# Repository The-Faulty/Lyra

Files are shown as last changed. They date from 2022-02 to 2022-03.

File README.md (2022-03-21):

# Lyra

**A SamD21 Based Rocket Deployment Altimeter**

This altimeter will be able to be used for single deployment events in mid to high power rocketry. A compact design was emphasized in order to allow for use in 24mm and larger body tubes, or attached to the parachute for a cable cutter or similar deployment method.

## Current State

As of right now, I am working on flight software with basic functionality. The original PCB design is filled with many flaws, however, I still included them for use as a reference. Plans have been made for a new version of the PCB to fix many, if not all, of the shortcomings my original design had. I believe I have found most of them, but one includes the difficulty of updating firmware and testing, which will inevitably lead to something being overlooked. Also to come are some pictures of the one prototype board that I have assembled. The changelog below is more to keep track of what I have or haven't tackled yet, so feel free to ignore it.

I have now successfully uploaded a version of the code to a Lyra board. One thing I did was replace the buzzer on the board with a bodged LED. This will allow for silent debugging and a guarantee that the lines are working. *This is the purpose of any digital writes to the buzzer pin.* The code that I uploaded ran until it attempted connection with the barometer in the setup. I will look further into the issue at a later point in time.

## The Bad, the Worse, and the Annoying

During my initial development of the Lyra pcb, I made some naive choices in terms of design, and overlooked other quality of life aspects which have led to many headaches during development. I'm going to go into some of the things that I have identified as issues in the current design or things I want to add in the next one.

The biggest issue that I made in the design of this pcb was not using a USB port. I figured that as long as I had the SWD I would be fine, but it just complicates development because I can't have the flash and SD card board attached at the same time. Another issue is lack of physical indicators. having LEDs on the power lines, pyro lines, and just attached to a GPIO pin would have helped a lot in diagnosing issues. Instead of using the BMP388, a barometer that I have used before and knew worked, I chose the MS5607 for Lyra. I don't remember why I made that choice, but the MS5607 has a few downsides compared to the BMP388. For one, there is no data ready register. This means that your code has to blindly wait for the reading to be completed, and then check back after. The libraries for using this sensor are also less tested than those for the BMP388. I also did not think very hard about the use of Lyra during an actual launch. I planned for the code to read a settings file from the SD card at launch, however, if I planned on using Lyra in multiple rockets or adjust settings on the go, I would have to bring a laptop. On the next itteration, one solution would be to use an oled shield, such as the adafruit feather oled, with a simple menu system for settings and readout. Finally, I wish I had broken out more pins to the daughter pcb. I didn't use all of the pins on the connector, and could have broken out I2C lines or similar for further prototyping.

## Changelog

Latest Changes:

**V0.2 - "Hands up, Don't Chute!"**

Notes: I think that most of the program is here, just need to do the loop logic. I also want to add data logging to the start of the flight.

- Fixed typo of `stateMacine` to `stateMachine`
- Fixed `state` being initialized as an integer instead of an instance of the `stateMachine` enum
- Fixed lack of function prototypes

- Changed `loop()` to use switch/case instead of `if else`
- Moved `readAlt()` to the start of if statement instead of in each case

- Added `ISDROGUE` and `ISAPOGEEDEPLOY` to user variables (I missed them in the last update)
- Added `DEPLOYALT` variable for setting the deployment altitude
- Added `SAVEDATA` boolean to toggle saving data to flash
- Added use of buzzer in `setup()` for indicating barometer found and setup complete
- Added `landed` case to `loop()`
- Added `rollPeriod` and `rollVelo` for use in velocity and acceleration calculations
- Added `calcAccel` for acceleration

**V0.1 - "No Function Junction"**

- Fixed variables being logged being out of order
- Fixed barometer code to use correct barometer model
- Fixed `readAlt()` function's for loop running until greater than the array's index
- Fixed not changing state from `startUp` to `idle` in setup

- Removed variable `rateLeng` and instead directly used the `rollAvg` array for vertical speed calculation

- Changed user-defined variables to be under define tags to allow usage in declaring array lengths

- Added vertical speed function (`getRate()`) and `avgRate` variable
- Added battery voltage function (`getBattVoltage()`)
- Added vertical speed to logging data
- Added `period` and `lastMillis` variables for tracking loop cycles
- Added majority of this ReadMe

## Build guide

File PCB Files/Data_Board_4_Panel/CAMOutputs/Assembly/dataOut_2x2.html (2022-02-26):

Partlist exported from C:/Users/andyd/Documents/EAGLE/projects/FC/Lyra/Panels/dataOut_2x2.sch at 10/29/2020 5:32 PM

Qty | Value | Device | Package | Parts | Description | BUILT_BY | COPYRIGHT | DESCRIPTION | DIGI-KEY_PART_NUMBER | MANUFACTURER_PART_NUMBER | MF | MP | PACKAGE | PROD_ID | PURCHASE-URL | SOURCELIBRARY | VALUE | VENDOR
4 | .1uF | 10NF-0603-50V-10% | 0603 | C1, C6, C8, C10 | 0.01uF/10nF/10,000pF ceramic capacitors | | | | | | | | | CAP-00867 | | | 10nF
4 | 10M | 220KOHM-0603-1/10W-1% | 0603 | R1, R3, R4, R5 | 220kΩ resistor | | | | | | | | | RES-08969 | | | 220k
4 | 12POS_HEADER | 12POS_HEADER | 12POS_HEADER | U$1, U$3, U$4, U$5
4 | 22pF | 10NF-0603-50V-10% | 0603 | C2, C5, C7, C9 | 0.01uF/10nF/10,000pF ceramic capacitors | | | | | | | | | CAP-00867 | | | 10nF
4 | 503182-1852 | 503182-1852 | MOLEX_503182-1852 | J1, J3, J4, J5 | Conn Micro SD Card M 8 POS 1.09mm Solder RA SMD Embossed T/R 0.5A/Contact | | | 10 (8 + 2) Position Card Connector microSD™ Surface Mount, Right Angle Gold | WM12834CT-ND | | Molex | 5031821852 | None | | https://pricing.snapeda.com/search/part/5031821852/?ref=eda
4 | S25FL064LABNFI043USON-8-M | S25FL064LABNFI043USON-8-M | USON-8-M | U1, U3, U4, U5 | | EMA_Jessica | Copyright (C) 2018 Accelerated Designs. All rights reserved | | | S25FL064LABNFI043 | | | | | | Cypress_Semiconductor_2019-12-17 | | Cypress Semiconductor

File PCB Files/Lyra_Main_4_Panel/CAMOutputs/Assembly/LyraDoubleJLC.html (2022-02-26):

Partlist exported from C:/Users/andyd/Documents/EAGLE/projects/FC/Lyra/Extras/LyraDoubleJLC.sch at 10/29/2020 7:39 AM

Qty | Value | Device | Package | Parts | Description | ARROW_ELECTRONICS-PURCHASE-URL | AVAILABILITY | BUILT_BY | COMMENT | COPYRIGHT | CUI_PURCHASE_URL | DESCRIPTION | DIGI-KEY_PART_NUMBER | DIGIKEY-PURCHASE-URL | EU_ROHS_COMPLIANCE | MANUFACTURER_PART_NUMBER | MF | MOUSER-PURCHASE-URL | MP | PACKAGE | PRICE | PROD_ID | PURCHASE-URL | SOURCELIBRARY | VALUE | VENDOR
20 | 0.1uF | 0.1UF-0603-25V-(+80/-20%) | 0603 | C1, C2, C4, C5, C8, C21, C22, C24, C25, C28, C41, C42, C44, C45, C48, C61, C62, C64, C65, C68 | 0.1µF ceramic capacitors | | | | | | | | | | | | | | | | | CAP-00810 | | | 0.1uF
4 | 0.22uF | 0.1UF-0603-25V-(+80/-20%) | 0603 | C3, C23, C43, C63 | 0.1µF ceramic capacitors | | | | | | | | | | | | | | | | | CAP-00810 | | | 0.1uF
8 | 1.0uF | 1.0UF-0402-16V-10% | 0402 | C11, C12, C29, C30, C49, C50, C69, C70 | 1µF ceramic capacitors | | | | | | | | | | | | | | | | | CAP-12417 | | | 1.0uF
4 | 100k | RESISTOR0402 | 0402 | R7, R27, R51, R75 | Generic Resistor Package
12 | 10k | RESISTOR0402 | 0402 | R4, R5, R9, R25, R29, R33, R49, R53, R57, R73, R77, R81 | Generic Resistor Package
4 | 12POS_SOCKET | 12POS_SOCKET | 12POS_SOCKET | U$5, U$15, U$25, U$35
4 | 180K | RESISTOR0402 | 0402 | R11, R35, R59, R83 | Generic Resistor Package
4 | 1k | RESISTOR0402 | 0402 | R8, R28, R52, R76 | Generic Resistor Package
8 | 20K | RESISTOR0402 | 0402 | R10, R12, R34, R36, R58, R60, R82, R84 | Generic Resistor Package
4 | 30 | RESISTOR0402 | 0402 | R1, R30, R54, R78 | Generic Resistor Package
4 | 32.768KHz | FC-135 | FC-135 | U$1, U$12, U$22, U$32
8 | 4.7k | 4.7KOHM-0603-1/10W-1% | 0603 | R2, R3, R31, R32, R55, R56, R79, R80 | 4.7kΩ resistor | | | | | | | | | | | | | | | | | RES-07857 | | | 4.7k
4 | 470k | RESISTOR0402 | 0402 | R6, R26, R50, R74 | Generic Resistor Package
8 | 7 pF | 0.1UF-0402-16V-10% | 0402 | C6, C7, C26, C27, C46, C47, C66, C67 | 0.1µF ceramic capacitors | | | | | | | | | | | | | | | | | CAP-12416 | | | 0.1uF
4 | ATSAMD21G18A-MU | ATSAMD21G18A-MU | QFN50P700X700X90-49N | U1, U5, U9, U13 | Cortex-M0+, 256KB FLASH, 32KB SRAM, USB, DMA, T&R - 48QFN IND TEMP, GREEN, 1.6-3.6V, 48MHz/ QFN (ZA) | https://snapeda.com/shop?store=Arrow+Electronics&id=590181 | | | | | | ARM® Cortex®-M0+ SAM D21G Microcontroller IC 32-Bit 48MHz 256KB (256K x 8) FLASH 48-QFN (7x7) | ATSAMD21G18A-MUTTR-ND | https://snapeda.com/shop?store=DigiKey&id=590181 | | | Microchip | https://snapeda.com/shop?store=Mouser&id=590181 | ATSAMD21G18A-MU | QFN-48 Microchip
4 | BUTTON | BUTTON | BUTTON | U$4, U$14, U$24, U$34
4 | CPT-1255C-090 | CPT-1255C-090 | CUI_CPT-1255C-090 | LS2, LS3, LS5, LS7 | Buzzer 12 mm, 20 Vp-p, 80 dB, Through Hole, Piezo Audio Transducer Buzzer Check prices | | Good | | | | https://www.cuidevices.com/product/audio/buzzers/audio-transducers/cpt-1255c-090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 | 12 mm, 20 Vp-p, 80 dB, Through Hole, Piezo Audio Transducer Buzzer | | | | | CUI Devices | | CPT-1255C-090 | CUI Inc. | None | | https://pricing.snapeda.com/search/part/CPT-1255C-090/?ref=eda
4 | IRLHM630PBF | IRLHM630PBF | IRLHM630PBF | U$2, U$11, U$21, U$31
4 | MS860702BA01-50 | MS860702BA01-50 | TE_MS860702BA01-50 | U3, U6, U10, U14 | Pressure Temp Humidity Sensor Buy Part | | Warning | | MS860702BA01-50 | | | PHT SENSOR, 29PSI-10MBAR, QFN-8 | | | Compliant | | TE Connectivity | https://snapeda.com/shop?store=Mouser&id=555057 | MS860702BA01-50 | QFN-8 TE Connectivity | None
4 | NCP718AMT330TBG | NCP718AMT330TBG | NCP718BMT330TBG | U$3, U$13, U$23, U$33
8 | OSTVN02A150 | OSTVN02A150 | CONN_OSTVN02A150_OST | J1, J2, J5, J6, J9, J10, J13, J14 | | | | EMA_Cory | | Copyright (C) 2018 Accelerated Designs. All rights reserved | | | | | | OSTVN02A150 | | | | | | | | On_Shore_Technology_2019-12-02 | | On Shore Technology Inc

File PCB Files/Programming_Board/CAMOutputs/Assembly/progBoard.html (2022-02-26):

Partlist exported from C:/Users/andyd/Documents/EAGLE/projects/FC/Lyra/progBoard.sch at 10/29/2020 12:00 AM

Qty | Value | Device | Package | Parts | Description | POPULARITY
1 | | PINHD-1X5 | 1X05 | JP2 | PIN HEADER | 69

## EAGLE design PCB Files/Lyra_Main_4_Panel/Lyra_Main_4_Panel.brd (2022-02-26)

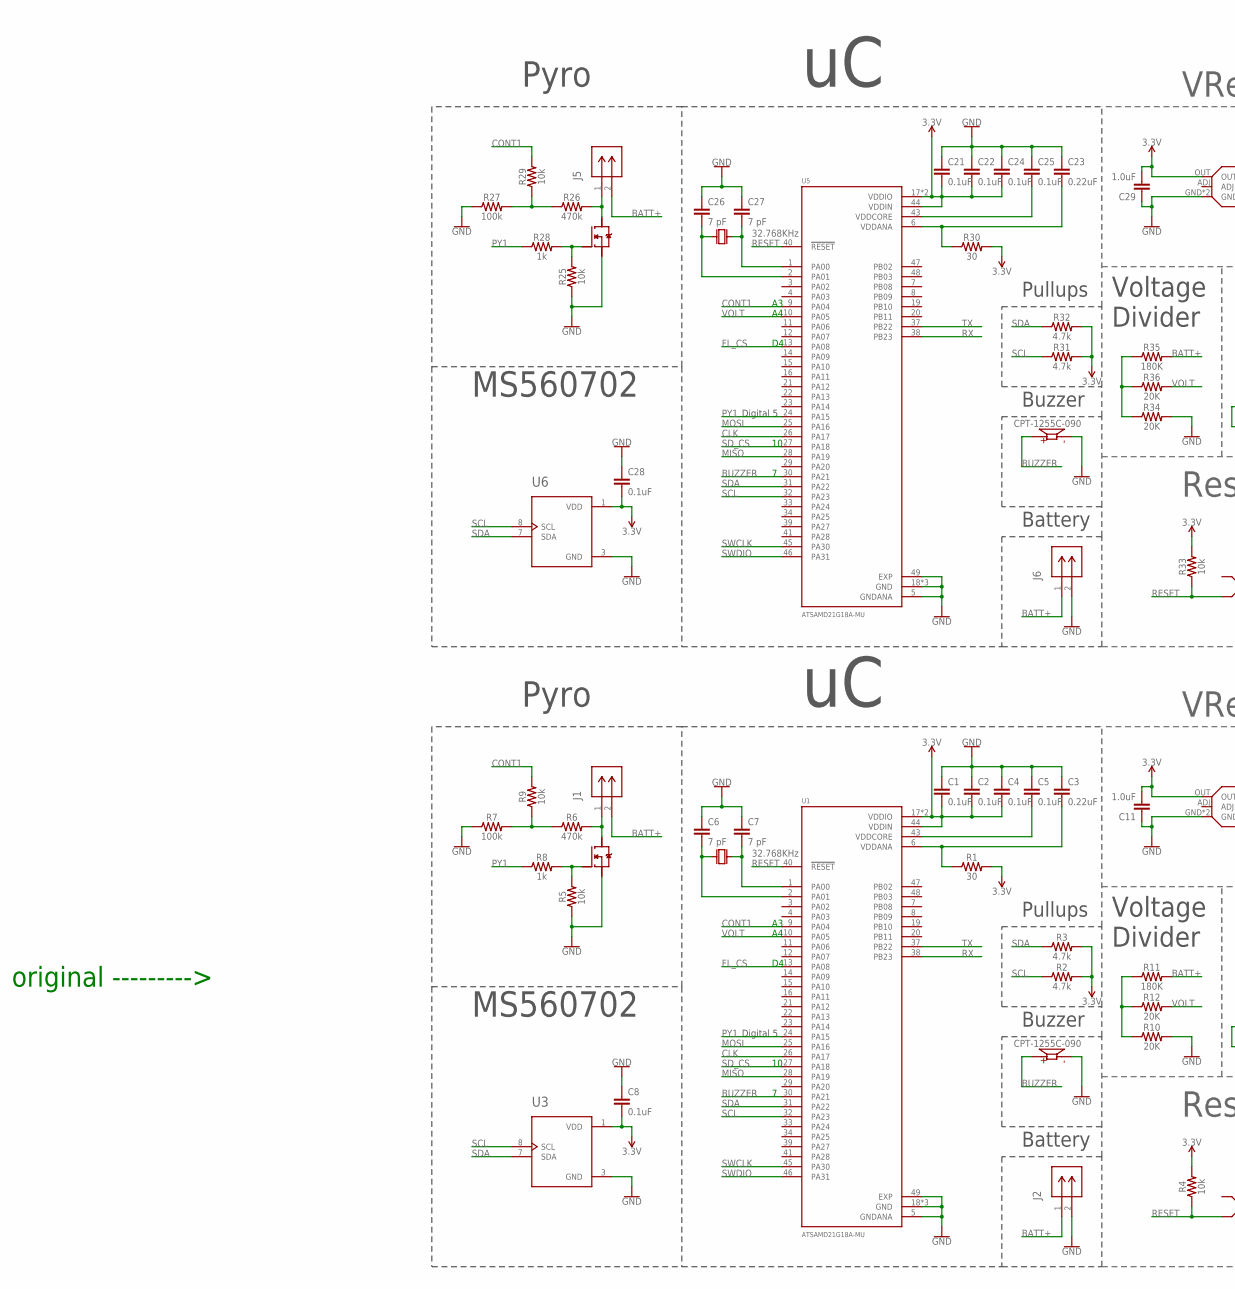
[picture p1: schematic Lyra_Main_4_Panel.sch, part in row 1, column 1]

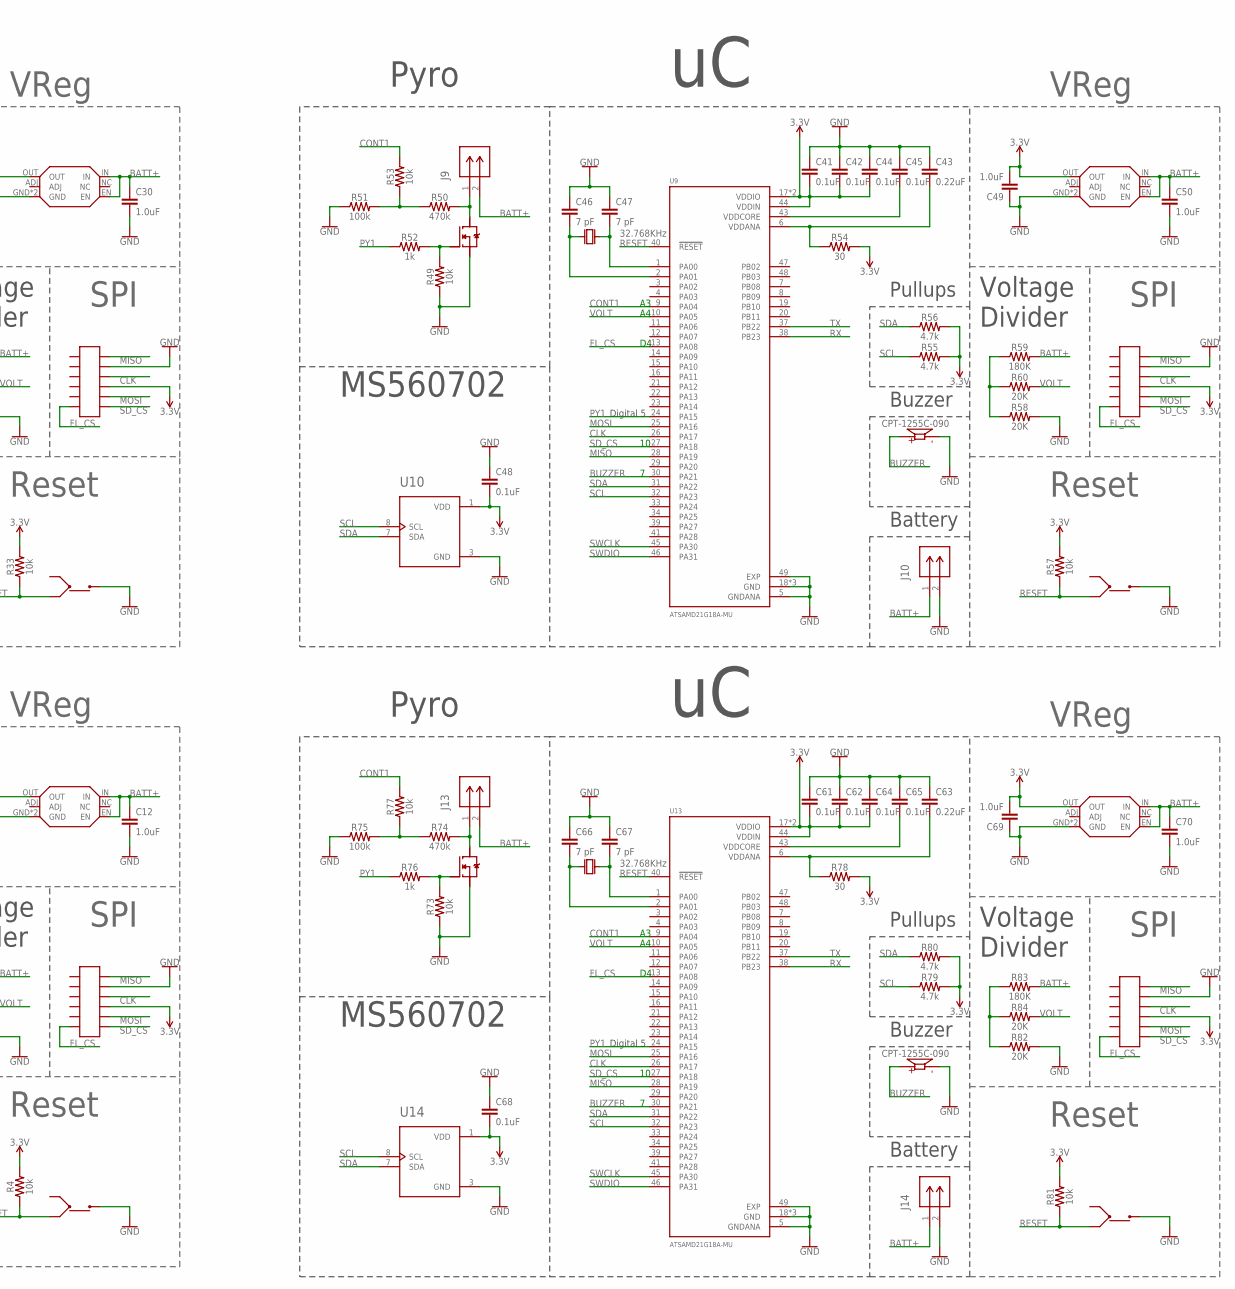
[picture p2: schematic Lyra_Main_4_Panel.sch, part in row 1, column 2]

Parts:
C1, C2, C4, C5, C8, C21, C22, C24, C25, C28, C41, C42, C44, C45, C48, C61, C62, C64, C65, C68: 0.1uF; 0603
C3, C23, C43, C63: 0.22uF; 0603
C6, C7, C26, C27, C46, C47, C66, C67: 7 pF; 0402
C11, C12, C29, C30, C49, C50, C69, C70: 1.0uF; 0402
J1, J2, J5, J6, J9, J10, J13, J14: OSTVN02A150; CONN_OSTVN02A150_OST
LS2, LS3, LS5, LS7: CPT-1255C-090; CUI_CPT-1255C-090
R1, R30, R54, R78: 30; 0402
R2, R3, R31, R32, R55, R56, R79, R80: 4.7k; 0603
R4, R5, R9, R25, R29, R33, R49, R53, R57, R73, R77, R81: 10k; 0402
R6, R26, R50, R74: 470k; 0402
R7, R27, R51, R75: 100k; 0402
R8, R28, R52, R76: 1k; 0402
R10, R12, R34, R36, R58, R60, R82, R84: 20K; 0402
R11, R35, R59, R83: 180K; 0402
U1, U5, U9, U13: ATSAMD21G18A-MU; QFN50P700X700X90-49N
U3, U6, U10, U14: MS860702BA01-50; TE_MS860702BA01-50
U$1, U$12, U$22, U$32: 32.768KHz; FC-135
U$2, U$11, U$21, U$31: IRLHM630PBF
U$3, U$13, U$23, U$33: NCP718AMT330TBG; NCP718BMT330TBG
U$4, U$14, U$24, U$34: BUTTON
U$5, U$15, U$25, U$35: 12POS_SOCKET

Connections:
3.3V: C1.2, C2.2, C4.2, C8.2, C11.2, C21.2, C22.2, C24.2, C28.2, C29.2, C41.2, C42.2, C44.2, C48.2, C49.2, C61.2, C62.2, C64.2, C68.2, C69.2, R1.2, R2.2, R3.2, R4.2, R30.2, R31.2, R32.2, R33.2, R54.2, R55.2, R56.2, R57.2, R78.2, R79.2, R80.2, R81.2, U1.17 (VDDIO), U1.36 (VDDIO), U1.44 (VDDIN), U3.1 (VDD), U5.17 (VDDIO), U5.36 (VDDIO), U5.44 (VDDIN), U6.1 (VDD), U9.17 (VDDIO), U9.36 (VDDIO), U9.44 (VDDIN), U10.1 (VDD), U13.17 (VDDIO), U13.36 (VDDIO), U13.44 (VDDIN), U14.1 (VDD), U$3.OUT, U$5.P$9, U$13.OUT, U$15.P$9, U$23.OUT, U$25.P$9, U$33.OUT, U$35.P$9
BATT+: C12.1, C30.1, C50.1, C70.1, J1.2, J2.1, J5.2, J6.1, J9.2, J10.1, J13.2, J14.1, R11.2, R35.2, R59.2, R83.2, U$3.EN, U$3.IN, U$13.EN, U$13.IN, U$23.EN, U$23.IN, U$33.EN, U$33.IN
BUZZER: LS2.P, LS3.P, LS5.P, LS7.P, U1.30 (PA21), U5.30 (PA21), U9.30 (PA21), U13.30 (PA21)
CLK: U1.26 (PA17), U5.26 (PA17), U9.26 (PA17), U13.26 (PA17), U$5.P$10, U$15.P$10, U$25.P$10, U$35.P$10
CONT1: R9.2, R29.2, R53.2, R77.2, U1.9 (PA04), U5.9 (PA04), U9.9 (PA04), U13.9 (PA04)
FL_CS: U1.13 (PA08), U5.13 (PA08), U9.13 (PA08), U13.13 (PA08), U$5.P$6, U$15.P$6, U$25.P$6, U$35.P$6
GND: C1.1, C2.1, C3.1, C4.1, C5.1, C6.1, C7.1, C8.1, C11.1, C12.2, C21.1, C22.1, C23.1, C24.1, C25.1, C26.1, C27.1, C28.1, C29.1, C30.2, C41.1, C42.1, C43.1, C44.1, C45.1, C46.1, C47.1, C48.1, C49.1, C50.2, C61.1, C62.1, C63.1, C64.1, C65.1, C66.1, C67.1, C68.1, C69.1, C70.2, J2.2, J6.2, J10.2, J14.2, LS2.N, LS3.N, LS5.N, LS7.N, R5.1, R7.1, R10.2, R25.1, R27.1, R34.2, R49.1, R51.1, R58.2, R73.1, R75.1, R82.2, U1.5 (GNDANA), U1.18 (GND), U1.35 (GND), U1.42 (GND), U1.49 (EXP), U3.3 (GND), U5.5 (GNDANA), U5.18 (GND), U5.35 (GND), U5.42 (GND), U5.49 (EXP), U6.3 (GND), U9.5 (GNDANA), U9.18 (GND), U9.35 (GND), U9.42 (GND), U9.49 (EXP), U10.3 (GND), U13.5 (GNDANA), U13.18 (GND), U13.35 (GND), U13.42 (GND), U13.49 (EXP), U14.3 (GND), U$2.P$2, U$2.P$3, U$2.P$4, U$3.GND, U$3.P$7 (GND), U$4.4 (OUT), U$5.P$11, U$11.P$2, U$11.P$3, U$11.P$4, U$13.GND, U$13.P$7 (GND), U$14.4 (OUT), U$15.P$11, U$21.P$2, U$21.P$3, U$21.P$4, U$23.GND, U$23.P$7 (GND), U$24.4 (OUT), U$25.P$11, U$31.P$2, U$31.P$3, U$31.P$4, U$33.GND, U$33.P$7 (GND), U$34.4 (OUT), U$35.P$11
MISO: U1.28 (PA19), U5.28 (PA19), U9.28 (PA19), U13.28 (PA19), U$5.P$12, U$15.P$12, U$25.P$12, U$35.P$12
MOSI: U1.25 (PA16), U5.25 (PA16), U9.25 (PA16), U13.25 (PA16), U$5.P$8, U$15.P$8, U$25.P$8, U$35.P$8
unnamed: C7.2, U1.1 (PA00), U$1.P$2
unnamed: J1.1, R6.2, U$2.P$5, U$2.P$6, U$2.P$7, U$2.P$8, U$2.P$9
unnamed: R5.2, R8.2, U$2.P$1
unnamed: C6.2, U1.2 (PA01), U$1.P$1
unnamed: R6.1, R7.2, R9.1
unnamed: R10.1, R11.1, R12.1
unnamed: C5.2, U1.43 (VDDCORE)
unnamed: C3.2, R1.1, U1.6 (VDDANA)
unnamed: J5.1, R26.2, U$11.P$5, U$11.P$6, U$11.P$7, U$11.P$8, U$11.P$9
unnamed: R25.2, R28.2, U$11.P$1
unnamed: R26.1, R27.2, R29.1
unnamed: C27.2, U5.1 (PA00), U$12.P$2
unnamed: C26.2, U5.2 (PA01), U$12.P$1
unnamed: C25.2, U5.43 (VDDCORE)
unnamed: C23.2, R30.1, U5.6 (VDDANA)
unnamed: R34.1, R35.1, R36.1
unnamed: J9.1, R50.2, U$21.P$5, U$21.P$6, U$21.P$7, U$21.P$8, U$21.P$9
unnamed: R49.2, R52.2, U$21.P$1
unnamed: R50.1, R51.2, R53.1
unnamed: C47.2, U9.1 (PA00), U$22.P$2
unnamed: C46.2, U9.2 (PA01), U$22.P$1
unnamed: C45.2, U9.43 (VDDCORE)
unnamed: C43.2, R54.1, U9.6 (VDDANA)
unnamed: R58.1, R59.1, R60.1
unnamed: J13.1, R74.2, U$31.P$5, U$31.P$6, U$31.P$7, U$31.P$8, U$31.P$9
unnamed: R73.2, R76.2, U$31.P$1
unnamed: R74.1, R75.2, R77.1
unnamed: C67.2, U13.1 (PA00), U$32.P$2
unnamed: C66.2, U13.2 (PA01), U$32.P$1
unnamed: C65.2, U13.43 (VDDCORE)
unnamed: C63.2, R78.1, U13.6 (VDDANA)
unnamed: R82.1, R83.1, R84.1
PY1: R8.1, R28.1, R52.1, R76.1, U1.24 (PA15), U5.24 (PA15), U9.24 (PA15), U13.24 (PA15)
RESET: R4.1, R33.1, R57.1, R81.1, U1.40 (!RESET), U5.40 (!RESET), U9.40 (!RESET), U13.40 (!RESET), U$4.2 (IN(2)), U$14.2 (IN(2)), U$24.2 (IN(2)), U$34.2 (IN(2))
RX: U1.38 (PB23), U5.38 (PB23), U9.38 (PB23), U13.38 (PB23)
SCL: R2.1, R31.1, R55.1, R79.1, U1.32 (PA23), U3.8 (SCL), U5.32 (PA23), U6.8 (SCL), U9.32 (PA23), U10.8 (SCL), U13.32 (PA23), U14.8 (SCL)
SDA: R3.1, R32.1, R56.1, R80.1, U1.31 (PA22), U3.7 (SDA), U5.31 (PA22), U6.7 (SDA), U9.31 (PA22), U10.7 (SDA), U13.31 (PA22), U14.7 (SDA)
SD_CS: U1.27 (PA18), U5.27 (PA18), U9.27 (PA18), U13.27 (PA18), U$5.P$7, U$15.P$7, U$25.P$7, U$35.P$7
SWCLK: U1.45 (PA30), U5.45 (PA30), U9.45 (PA30), U13.45 (PA30)
SWDIO: U1.46 (PA31), U5.46 (PA31), U9.46 (PA31), U13.46 (PA31)
TX: U1.37 (PB22), U5.37 (PB22), U9.37 (PB22), U13.37 (PB22)
VOLT: R12.2, R36.2, R60.2, R84.2, U1.10 (PA05), U5.10 (PA05), U9.10 (PA05), U13.10 (PA05)

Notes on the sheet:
Pyro
Buzzer
Battery
MS560702
Pullups
VReg
SPI
Reset
Digital 5
Voltage Divider
original --------->

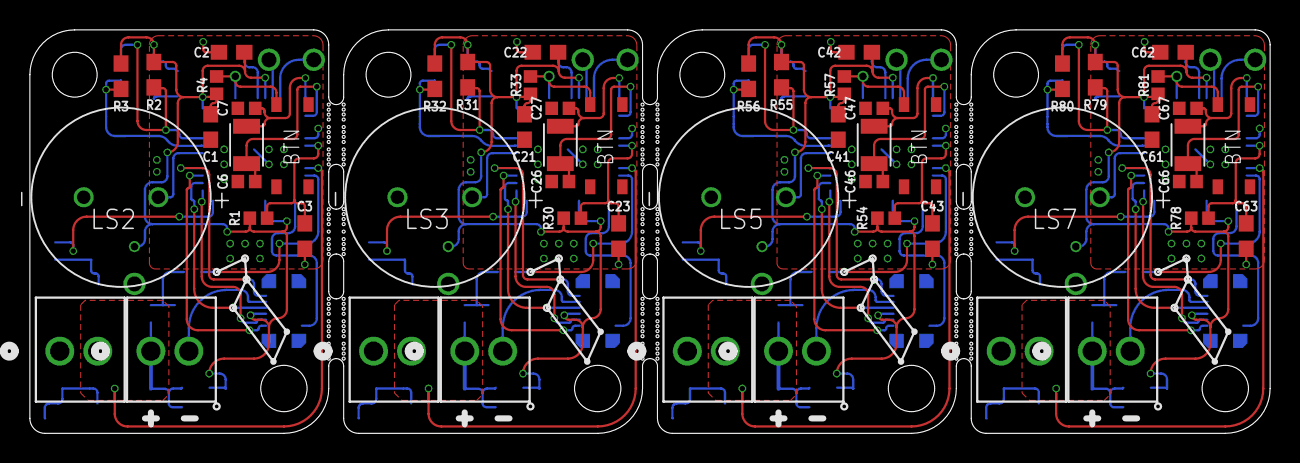
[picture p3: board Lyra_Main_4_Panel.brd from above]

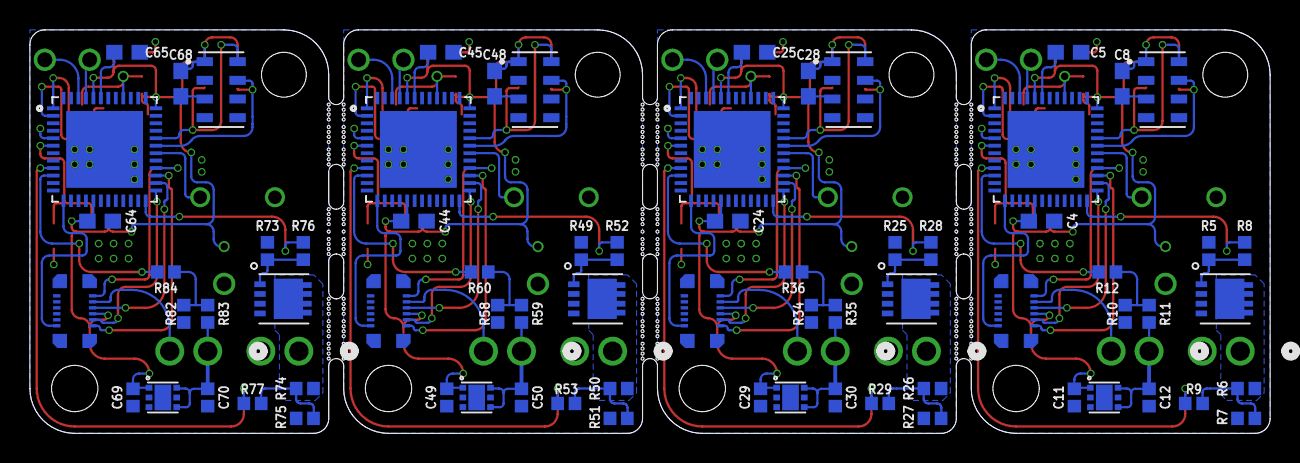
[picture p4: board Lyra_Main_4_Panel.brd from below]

Board: 2 copper layers, 83.0 x 27.0 mm, 128 parts (72 on the bottom side), 51 nets.

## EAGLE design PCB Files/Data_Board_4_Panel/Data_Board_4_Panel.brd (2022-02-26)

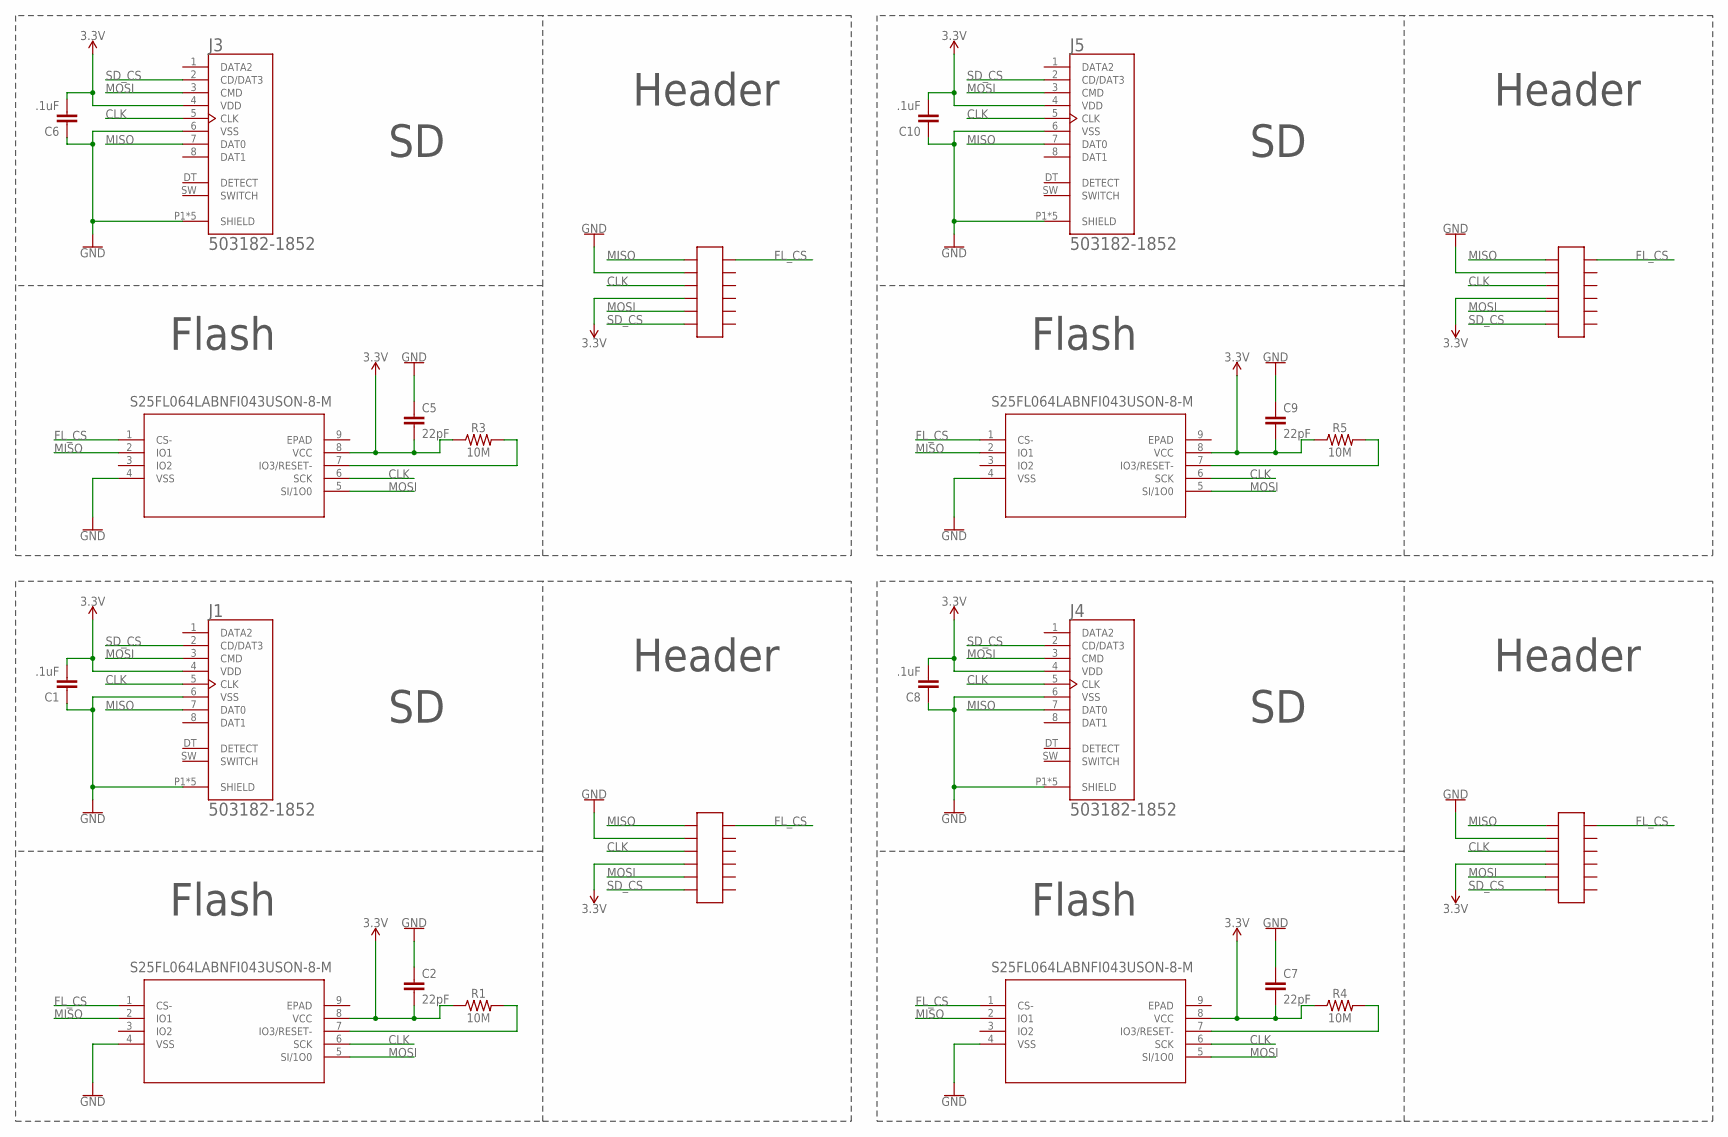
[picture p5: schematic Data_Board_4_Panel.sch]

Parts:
C1, C6, C8, C10: .1uF; 0603
C2, C5, C7, C9: 22pF; 0603
J1, J3, J4, J5: 503182-1852; MOLEX_503182-1852
R1, R3, R4, R5: 10M; 0603
U1, U3, U4, U5: S25FL064LABNFI043USON-8-M; USON-8-M
U$1, U$3, U$4, U$5: 12POS_HEADER

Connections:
3.3V: C1.2, C2.2, C5.2, C6.2, C7.2, C8.2, C9.2, C10.2, J1.4 (VDD), J3.4 (VDD), J4.4 (VDD), J5.4 (VDD), R1.1, R3.1, R4.1, R5.1, U1.8 (VCC), U3.8 (VCC), U4.8 (VCC), U5.8 (VCC), U$1.P$4, U$3.P$4, U$4.P$4, U$5.P$4
CLK: J1.5 (CLK), J3.5 (CLK), J4.5 (CLK), J5.5 (CLK), U1.6 (SCK), U3.6 (SCK), U4.6 (SCK), U5.6 (SCK), U$1.P$3, U$3.P$3, U$4.P$3, U$5.P$3
FL_CS: U1.1 (CS-), U3.1 (CS-), U4.1 (CS-), U5.1 (CS-), U$1.P$12, U$3.P$12, U$4.P$12, U$5.P$12
GND: C1.1, C2.1, C5.1, C6.1, C7.1, C8.1, C9.1, C10.1, J1.6 (VSS), J1.P1 (SHIELD), J1.P2 (SHIELD), J1.P3 (SHIELD), J1.P4 (SHIELD), J1.P5 (SHIELD), J3.6 (VSS), J3.P1 (SHIELD), J3.P2 (SHIELD), J3.P3 (SHIELD), J3.P4 (SHIELD), J3.P5 (SHIELD), J4.6 (VSS), J4.P1 (SHIELD), J4.P2 (SHIELD), J4.P3 (SHIELD), J4.P4 (SHIELD), J4.P5 (SHIELD), J5.6 (VSS), J5.P1 (SHIELD), J5.P2 (SHIELD), J5.P3 (SHIELD), J5.P4 (SHIELD), J5.P5 (SHIELD), U1.4 (VSS), U3.4 (VSS), U4.4 (VSS), U5.4 (VSS), U$1.P$2, U$3.P$2, U$4.P$2, U$5.P$2
MISO: J1.7 (DAT0), J3.7 (DAT0), J4.7 (DAT0), J5.7 (DAT0), U1.2 (IO1), U3.2 (IO1), U4.2 (IO1), U5.2 (IO1), U$1.P$1, U$3.P$1, U$4.P$1, U$5.P$1
MOSI: J1.3 (CMD), J3.3 (CMD), J4.3 (CMD), J5.3 (CMD), U1.5 (SI/1O0), U3.5 (SI/1O0), U4.5 (SI/1O0), U5.5 (SI/1O0), U$1.P$5, U$3.P$5, U$4.P$5, U$5.P$5
unnamed: R3.2, U3.7 (IO3/RESET-)
unnamed: R4.2, U4.7 (IO3/RESET-)
unnamed: R5.2, U5.7 (IO3/RESET-)
unnamed: R1.2, U1.7 (IO3/RESET-)
SD_CS: J1.2 (CD/DAT3), J3.2 (CD/DAT3), J4.2 (CD/DAT3), J5.2 (CD/DAT3), U$1.P$6, U$3.P$6, U$4.P$6, U$5.P$6

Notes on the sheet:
Flash
Header

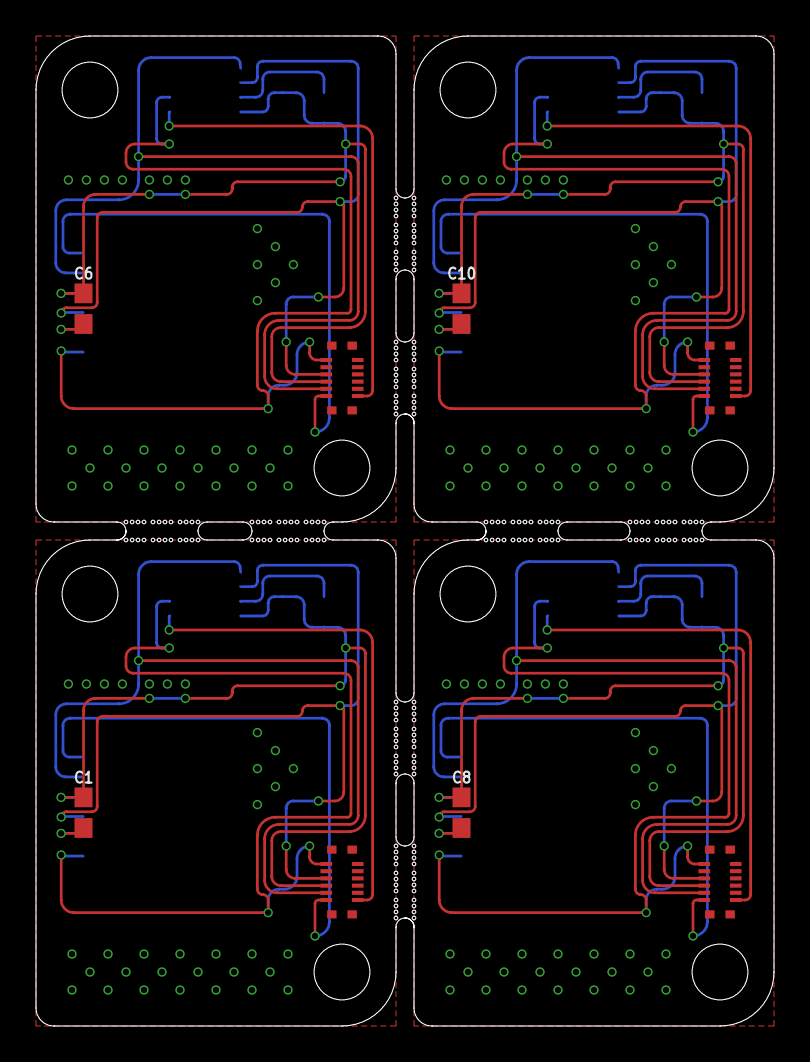
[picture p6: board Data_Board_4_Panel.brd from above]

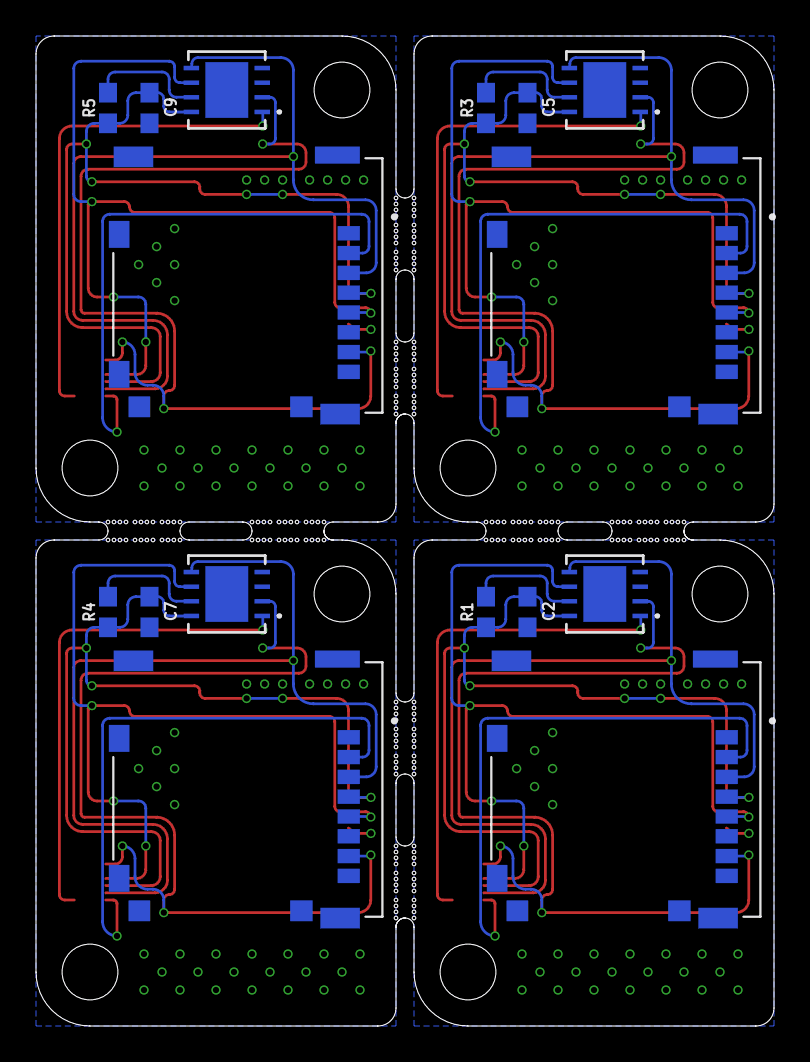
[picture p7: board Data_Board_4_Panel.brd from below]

Board: 2 copper layers, 41.0 x 55.0 mm, 24 parts (16 on the bottom side), 11 nets.

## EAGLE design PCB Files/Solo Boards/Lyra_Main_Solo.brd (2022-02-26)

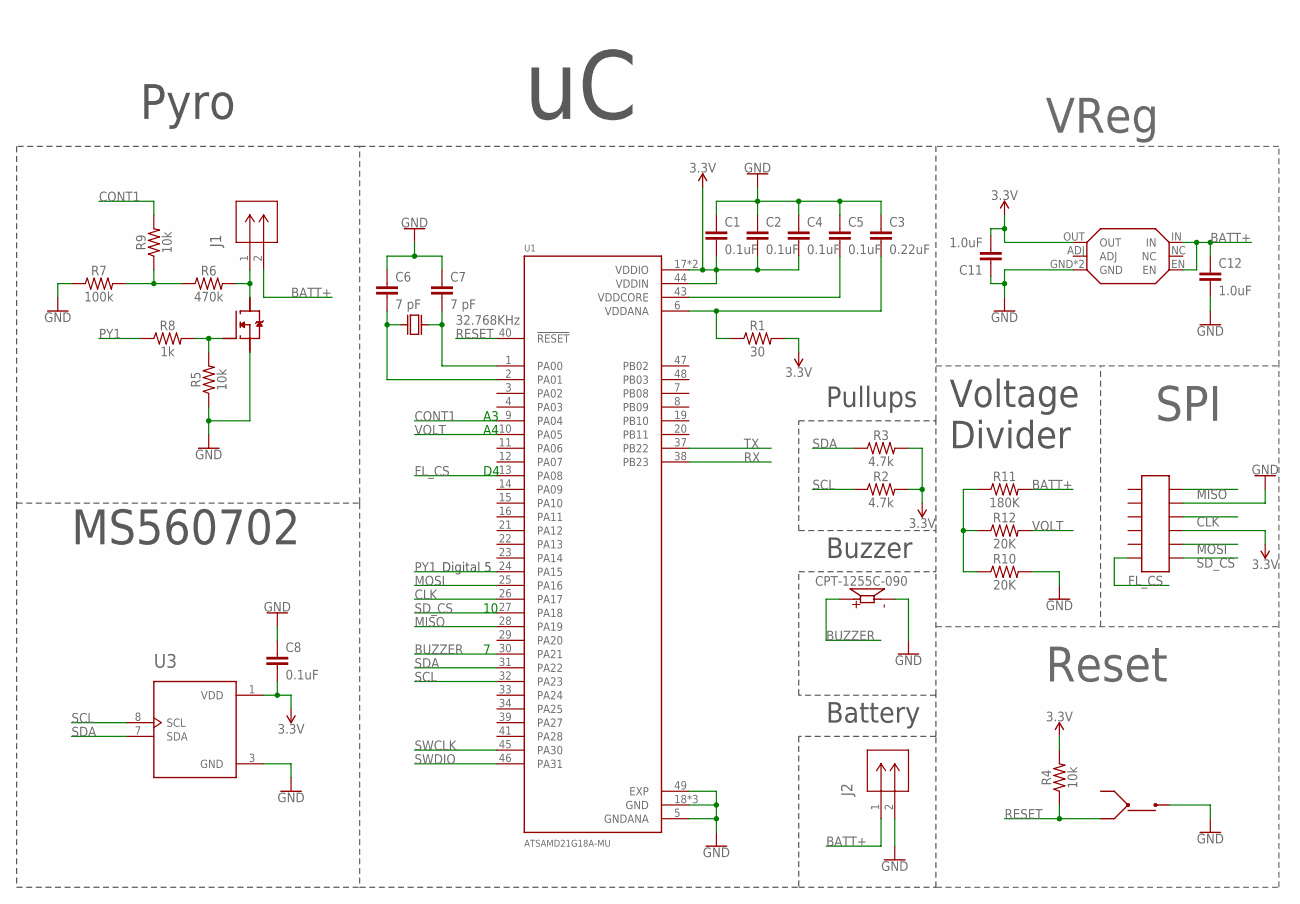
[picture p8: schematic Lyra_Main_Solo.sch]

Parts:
C1, C2, C4, C5, C8: 0.1uF; 0603
C3: 0.22uF; 0603
C6, C7: 7 pF; 0402
C11, C12: 1.0uF; 0402
J1, J2: OSTVN02A150; CONN_OSTVN02A150_OST
LS2: CPT-1255C-090; CUI_CPT-1255C-090
R1: 30; 0402
R2, R3: 4.7k; 0603
R4, R5, R9: 10k; 0402
R6: 470k; 0402
R7: 100k; 0402
R8: 1k; 0402
R10, R12: 20K; 0402
R11: 180K; 0402
U1: ATSAMD21G18A-MU; QFN50P700X700X90-49N
U3: MS860702BA01-50; TE_MS860702BA01-50
U$1: 32.768KHz; FC-135
U$2: IRLHM630PBF
U$3: NCP718AMT330TBG; NCP718BMT330TBG
U$4: BUTTON
U$5: 12POS_SOCKET

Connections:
3.3V: C1.2, C2.2, C4.2, C8.2, C11.2, R1.2, R2.2, R3.2, R4.2, U1.17 (VDDIO), U1.36 (VDDIO), U1.44 (VDDIN), U3.1 (VDD), U$3.OUT, U$5.P$9
BATT+: C12.1, J1.2, J2.1, R11.2, U$3.EN, U$3.IN
BUZZER: LS2.P, U1.30 (PA21)
CLK: U1.26 (PA17), U$5.P$10
CONT1: R9.2, U1.9 (PA04)
FL_CS: U1.13 (PA08), U$5.P$6
GND: C1.1, C2.1, C3.1, C4.1, C5.1, C6.1, C7.1, C8.1, C11.1, C12.2, J2.2, LS2.N, R5.1, R7.1, R10.2, U1.5 (GNDANA), U1.18 (GND), U1.35 (GND), U1.42 (GND), U1.49 (EXP), U3.3 (GND), U$2.P$2, U$2.P$3, U$2.P$4, U$3.GND, U$3.P$7 (GND), U$4.4 (OUT), U$5.P$11
MISO: U1.28 (PA19), U$5.P$12
MOSI: U1.25 (PA16), U$5.P$8
unnamed: C7.2, U1.1 (PA00), U$1.P$2
unnamed: J1.1, R6.2, U$2.P$5, U$2.P$6, U$2.P$7, U$2.P$8, U$2.P$9
unnamed: R5.2, R8.2, U$2.P$1
unnamed: C6.2, U1.2 (PA01), U$1.P$1
unnamed: R6.1, R7.2, R9.1
unnamed: R10.1, R11.1, R12.1
unnamed: C5.2, U1.43 (VDDCORE)
unnamed: C3.2, R1.1, U1.6 (VDDANA)
PY1: R8.1, U1.24 (PA15)
RESET: R4.1, U1.40 (!RESET), U$4.2 (IN(2))
RX: U1.38 (PB23)
SCL: R2.1, U1.32 (PA23), U3.8 (SCL)
SDA: R3.1, U1.31 (PA22), U3.7 (SDA)
SD_CS: U1.27 (PA18), U$5.P$7
SWCLK: U1.45 (PA30)
SWDIO: U1.46 (PA31)
TX: U1.37 (PB22)
VOLT: R12.2, U1.10 (PA05)

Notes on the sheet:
Pyro
Buzzer
Battery
MS560702
Pullups
VReg
SPI
Reset
Digital 5
Voltage Divider

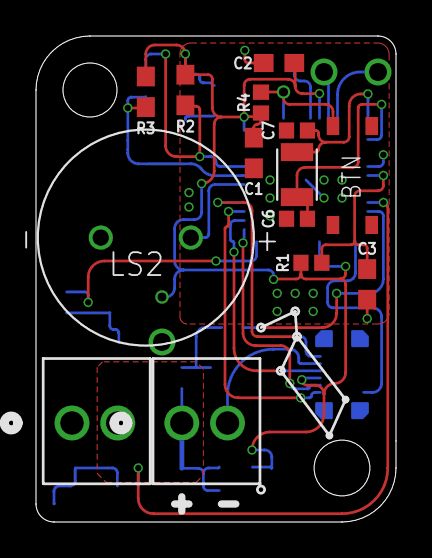
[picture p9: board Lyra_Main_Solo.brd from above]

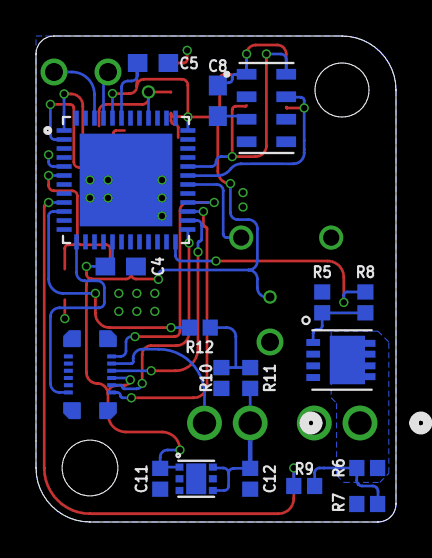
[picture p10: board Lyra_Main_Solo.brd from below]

Board: 2 copper layers, 20.0 x 27.0 mm, 32 parts (18 on the bottom side), 23 nets.

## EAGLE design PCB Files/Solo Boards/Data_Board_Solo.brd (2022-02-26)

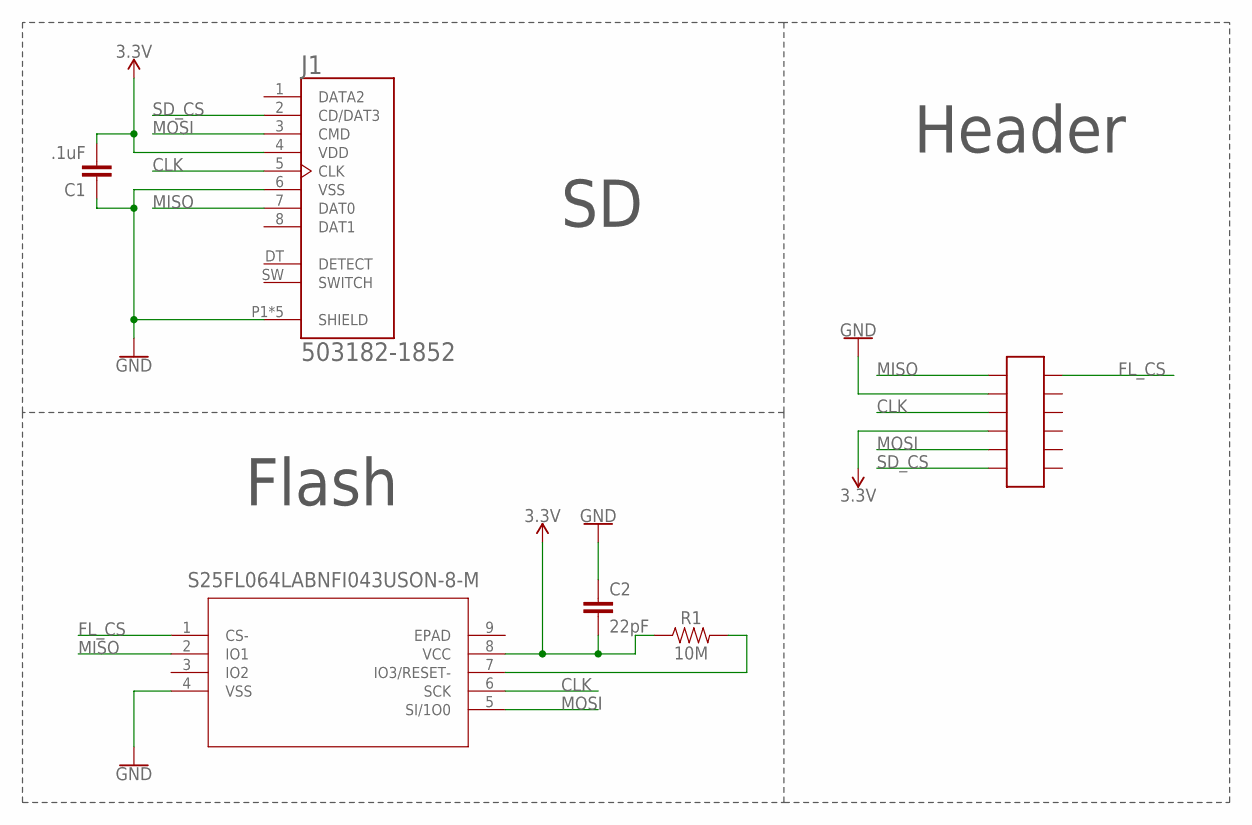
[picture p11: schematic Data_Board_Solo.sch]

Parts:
C1: .1uF; 0603
C2: 22pF; 0603
J1: 503182-1852; MOLEX_503182-1852
R1: 10M; 0603
U1: S25FL064LABNFI043USON-8-M; USON-8-M
U$1: 12POS_HEADER

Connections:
3.3V: C1.2, C2.2, J1.4 (VDD), R1.1, U1.8 (VCC), U$1.P$4
CLK: J1.5 (CLK), U1.6 (SCK), U$1.P$3
FL_CS: U1.1 (CS-), U$1.P$12
GND: C1.1, C2.1, J1.6 (VSS), J1.P1 (SHIELD), J1.P2 (SHIELD), J1.P3 (SHIELD), J1.P4 (SHIELD), J1.P5 (SHIELD), U1.4 (VSS), U$1.P$2
MISO: J1.7 (DAT0), U1.2 (IO1), U$1.P$1
MOSI: J1.3 (CMD), U1.5 (SI/1O0), U$1.P$5
unnamed: R1.2, U1.7 (IO3/RESET-)
SD_CS: J1.2 (CD/DAT3), U$1.P$6

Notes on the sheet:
Flash
Header

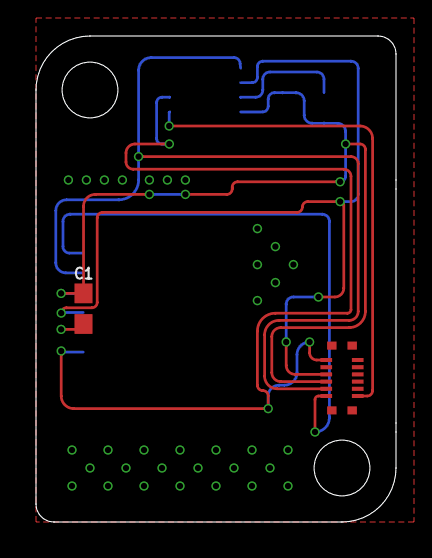
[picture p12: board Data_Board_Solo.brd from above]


Board: 2 copper layers, 20.0 x 27.0 mm, 6 parts (4 on the bottom side), 8 nets.

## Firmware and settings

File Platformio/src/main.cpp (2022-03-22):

/*
  Lyra barometric rocketry deployment computer
*/

#include <Arduino.h>
#include <vars.h>

void setup() {
  state = startUp;

  pinMode(VOLT, INPUT);
  pinMode(BUZZER, OUTPUT);

  //USING DIGITAL WRITE TO CONTROL AN LED THAT WAS BODGED ONTO THE PIN
  //tone(BUZZER, NOTE_E7, 200);
  digitalWrite(BUZZER, HIGH);
  delay(500);
  digitalWrite(BUZZER, LOW);

  do {
    //tone(BUZZER, NOTE_C7, 200);
    digitalWrite(BUZZER, HIGH);
    delay(500);
    digitalWrite(BUZZER, LOW);
    delay(500);
  } while (baro.connect() > 0);

  baro.setSamples(MS5xxx_CMD_ADC_2048);
  baro.setPressPa();                      //Set pressure readings to pascals (my preference and needed for the offset)
  baro.setDelay(50);

  //Set the launch site offset
  baro.checkUpdates();
  while (!baro.isReady()); // just waiting for the readings
  gndPres = baro.GetPres();
  baro.setPOffset(gndPres);

  flash.begin();
  SD.begin(SD_CS);

  tone(BUZZER, NOTE_E7, 100);
  delay(100);
  tone(BUZZER, NOTE_E7, 100);

  //Startup Complete!

  state = idle;
}

void loop() {
  period = millis() - lastMillis;
  lastMillis = millis();

  if (millis() - lastReadingMillis >= 40) { 
    baro.checkUpdates();
    lastReadingMillis = millis();
  }
  if (baro.isReady()) {
    readAlt();
    calcRate();
    switch (state) {
      case idle:
        //should I put some logging in here? not really sure, I'll come back to it
        if (avgAlt > MINALT) state = liftOff;
        break;
      case liftOff:
        logData();
        //detect burnout
        break;
      case burnOut:
        if (isApogee()) state = apogee;
        break;
      case apogee:
        //should this really be a state? maybe a boolean would fit better idk
        break;
      case descent:
        //do stuff for average descent rate ---- make a descent rate function?
        break;
      case drogue:
        //more descent rate calculations
        break;
      case mains:
        //some detect landing function
        break;
      case landed:
        //finalize stuff
        break;
    }
  }
} 

void readAlt() {
  curAlt = baro.getAltitude(true);
  avgAlt += curAlt;

  int bufferAlt[ROLLAVGLENG], bufferPeriod[ROLLAVGLENG];
  bufferAlt[0] = curAlt;
  bufferPeriod[0] = millis() - lastReadingMillis;

  for (int i = 0; i < ROLLAVGLENG; i++) {
    bufferAlt[i + 1] = rollAvg[i];
    bufferPeriod[i + 1] = rollPeriod[i];
    avgAlt += rollAvg[i];
  }
  memcpy(rollAvg, bufferAlt, sizeof(bufferAlt));
  memcpy(rollPeriod, bufferPeriod, sizeof(bufferPeriod));

  avgAlt /= ROLLAVGLENG - 1;
}

void calcRate() {
  for (int i = 1; i < ROLLAVGLENG - 1; i++) {
    rollVelo[i - 1] = (rollAvg[0] - rollAvg[ROLLAVGLENG - 1]) / (rollPeriod[i] / 1000);
    avgRate += rollVelo[i - 1];
  }

  avgRate /= ROLLAVGLENG - 1;
}

void calcAccel() {
  for (int i = 1; i < ROLLAVGLENG - 2; i++) {
    avgAccel += (rollVelo[0] - rollVelo[ROLLAVGLENG - 1]) / (((rollPeriod[i] + rollPeriod[i + 1]) / 2) / 1000);
  }

  avgAccel /= ROLLAVGLENG - 2;
}

byte getBattVoltage() {   //This doesnt need to be a function, but I think it will aid in code readability so why not
  return (byte) map(analogRead(VOLT), 0, 1023, 0, 8.4) * 10;
}

bool isApogee() {
  if (avgAlt > maxAlt) maxAlt = avgAlt;
  if (avgAlt < maxAlt) timesLessThan += 1;
  else timesLessThan = 0;
  if (timesLessThan >= 10) return true;
  else return false;
}

void logData() {
  Logger d = {
    (int) (curPress * 1000),
    (int) (curAlt * 1000),
    (int) (avgAlt * 1000),
    (int) (avgRate * 1000),
    (int) (avgAccel * 1000),
    state,
    getBattVoltage(),
    millis()
  };

  flash.writeAnything(flashIndex, d);
  flashIndex += sizeof(d);
}

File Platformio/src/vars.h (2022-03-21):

#include <Wire.h>
#include <SPI.h>
#include <MS5x.h>
#include <SPIMemory.h>
#include <SD.h>
#include <SDU.h>
#include <errors.h>

#define CONT1 A3
#define VOLT A4
#define FL_CS 4
#define PY1 5
#define BUZZER 7
#define SD_CS 10

//User defined variables
#define MINALT 200                                                          //Minimum altitude for flight detection
#define ROLLAVGLENG 10                                                      //Defines the length of the roling average
#define ISDROGUE false                                                      //Set true if using Lyra to deploy drogue chutes
#define ISAPOGEEDEPLOY false                                                //Set true if you want Lyra to deploy parachutes at apogee
#define DEPLOYALT 500                                                       //Sets the deployment altitude, ignore if using apogee deployment
#define SAVEDATA false                                                      //Mainly for testing purposes

MS5x baro(&Wire);
SPIFlash flash;
File myFile;

int period;                                                                 //Period between program loops
int lastMillis;                                                             //Last time loop was run
int rollPeriod[ROLLAVGLENG];                                                //Period between readings for velocity purposes
int lastReadingMillis;                                                      //Last time a reading was taken

float gndPres;                                                              //Pressure at the launch site ground
float curAlt;                                                               //Current altitude
float curPress;                                                             //Current pressure
float rollAvg[ROLLAVGLENG];                                                 //Used to take a rolling average of altitude data
float rollVelo[ROLLAVGLENG - 1];                                            //Used for acceleration calculations

float maxAlt;                                                               //Stores the max altitude 
float avgAlt;                                                               //Altitude after using the rolling average
float avgRate;                                                              //Average Vertical speed
float avgAccel;                                                             //Average vertical acceleration
int rollIndex = 0;                                                          //Used to loop through the 
int timesLessThan = 0;                                                      //Used to ensure apogee has been reached, when over 10

uint32_t flashIndex = 0;                                                    //Index where to write data to flash

//Function Prototypes
void readAlt();
void calcRate();
void calcAccel();
void logData();
bool isApogee();
byte getBattVoltage();

enum stateMachine {                                                         //State machine 
  startUp,
  idle,
  liftOff,
  burnOut,
  apogee,
  descent,
  drogue,
  mains,
  landed
};
stateMachine state;

#pragma pack(1)                                                             //tells compiler to pack the variables together with no weird spacing issues that there would otherwise be

struct LoggerVars {                                                         //Struct for data logging
  int pressure;
  int alt;
  int filtAlt;
  int rate;
  int accel;
  byte curState;
  byte battVolt;
  uint32_t time;
};

union Logger {
  LoggerVars vars;
  char raw[sizeof(LoggerVars)];
};

#pragma pack(0)                                                             //compiler can go back to normal

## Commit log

2022-02-26 Initial commit
    PCB files and early code
    Plenty of work to be done on software end. Possible PCB v2 to improve on many of the weak points of v1 design.
    [Data_Board_4_Panel.brd, Data_Board_4_Panel.sch, Data_Board_Solo.brd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]
2022-03-08 V0.1 - "No Function Junction"
    Just minor additions to the code as well as fixes and lots of thinking to do.
    [main.cpp, vars.h]
2022-03-21 Update main.cpp
    Quick syntax fix
    [main.cpp]
2022-03-22 Quick Fix: Added rollVelo into calcRate function
    [main.cpp]

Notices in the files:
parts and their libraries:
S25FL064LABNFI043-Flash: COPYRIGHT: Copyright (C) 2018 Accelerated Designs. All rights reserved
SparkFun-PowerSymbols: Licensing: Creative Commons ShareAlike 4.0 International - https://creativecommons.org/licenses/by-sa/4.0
